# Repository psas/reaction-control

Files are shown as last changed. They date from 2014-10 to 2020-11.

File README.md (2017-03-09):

reaction-control
================

## Overview
We want active stabilization for LV3, but wish to escape the vexxing dynamic pressure limitations of the present aerodyamic canard based [roll-control system](https://github.com/psas/roll-control) used on LV2.3.

The concept:
* Cold-gas rocket propulsion
* 8 N thrust (roll), 11 N (pitch x, y)
* Nitrogen tank at 4500 psi
* 8x 3D-printed bell nozzles
* PWM throttling
* "Robust control"

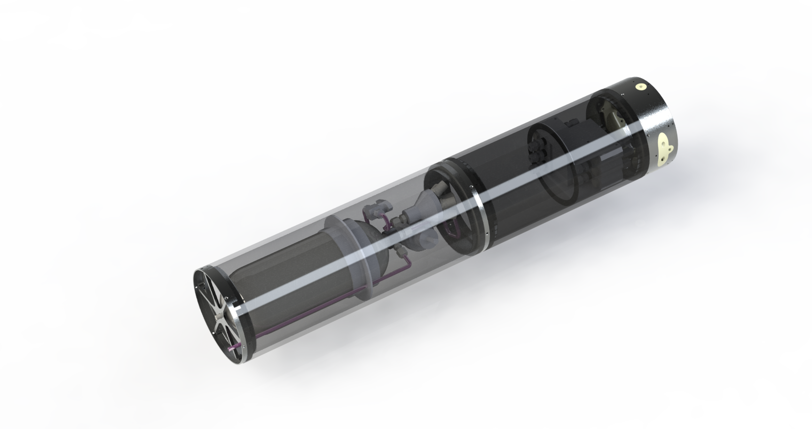
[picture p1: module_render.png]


Rao bells (e.g. nearly ideal nozzles) are hard to machine c.f. conical nozzles, but easy to 3D print. This also enables “plug & play” optimal expansion ratios for any trajectory. Here is the basic workflow:
* Determine flight envelope from simulation (for instance, using [OpenRocket](https://github.com/psas/lv3.0-airframe/tree/master/sim/ORK))
* Run `nozzle_sizing.m` script to determine nozzle design parameters
* Plug expansion ratio into parametric solid model and export `.stl`
* Print nozzles, install in carrier ring
* ???
* Fly!

This repo includes mathematical models, matlab and python controller scripts, eagle files for a custom MOSFET relay board, solenoid PWD test data for transfer functions, system test data and bode analysis, and the Solidworks CAD assembly for the LV3 Reaction Control System.

## Suplimentary Links
[Link to AIAA SPACE 2015 presentation slides](https://docs.google.com/presentation/d/1vfhgjRymidfKbpzjqC0tfAL57iSsNFOEQSFTw5_EEGs/edit?usp=sharing)

[Link to AIAA SPACE 2015 conference proceedings paper](https://github.com/psas/reaction-control/blob/master/pubs/AIAA%20RCS%20Manuscript_FINAL2.pdf)

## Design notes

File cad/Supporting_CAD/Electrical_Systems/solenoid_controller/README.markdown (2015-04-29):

# Solenoid Controller Board

A breakout board to drive the solenoids with GPIO from any microcrontroller.

## Schematic

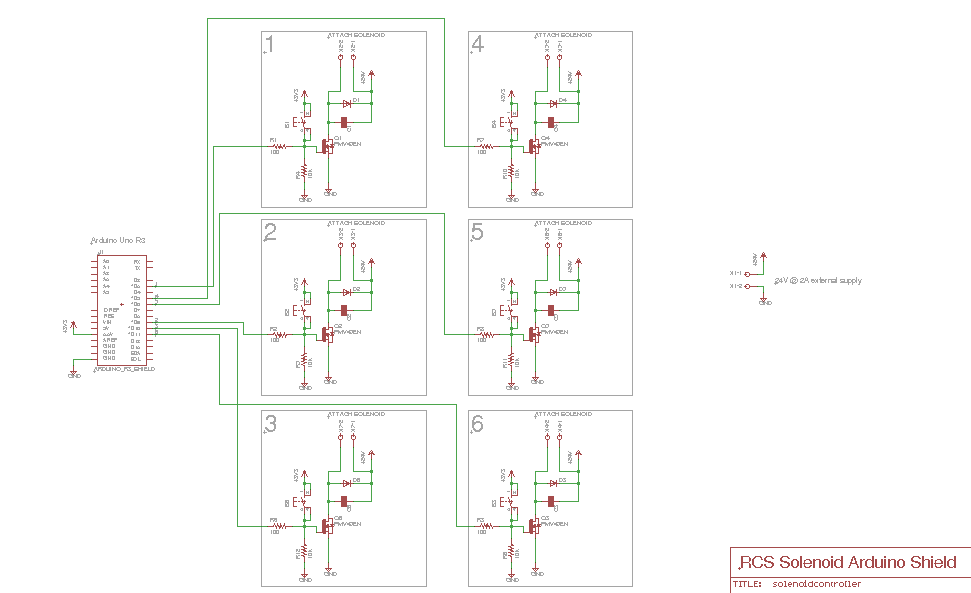
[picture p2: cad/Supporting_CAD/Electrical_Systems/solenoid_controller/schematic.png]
schematic


## Board

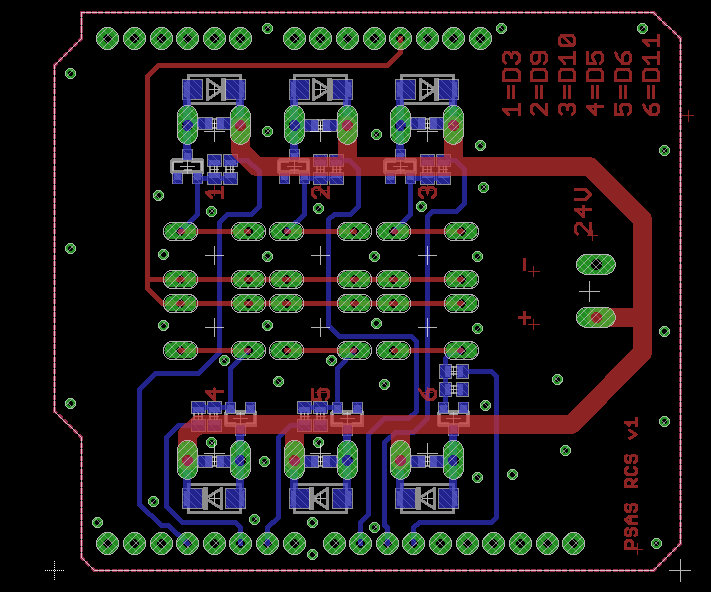
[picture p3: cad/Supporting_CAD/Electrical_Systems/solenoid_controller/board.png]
board


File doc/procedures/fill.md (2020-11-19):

# RCS Fill Procedure
## Notes
- The fill system definitely needs a choke to prevent over-filling the RCS and reduce the fill rate.
    - We may want to put a cold sink on that choke and monitor its temperature during testing.
- We probably want to define a standard way to clean fittings and dust covers,
  so we aren't repeating it in the procedure.
## Nomenclature
- "Caution" = potential damage to equipment
- "Danger" = potential damage to people (and potentially equipment).
- "FOD" = Foreign Object Debris (anything that shouldn't be there, e.g., dirt, metal shavings, grease, water, stray tools)
- "PPE" = Personal Protective Equipment
- "NOID" = NO IDentifier
    - Anything marked with NOID needs an identifier in the procedure and system-level illustration.

## Required Materials
| Quantity | Part Name | Identifier | Part Number
| --- | --- | --- | ---
| 1 | Compressed Gaseous Nitrogen Tank |  |  
| 1 | RCS Fill System |  |  
| 1 | impact-resistant safety goggles (TODO: ANSI standard) |  |  
| 1 | heavy hearing protection (TODO: ANSI standard) |  |  
| 1 | dry cloth |  |  
| 1 | fill tank transportation cart |  |  
| 1 |  |  |  
| 1 |  |  |  
| 1 |  |  |  
| 1 |  |  |  

## General Precautions
- The internal components of the RCS and its fill system are sensitive to FOD.
    - It's important to keep work areas clean to avoid contamination.
- The fill tank is nominally pressurized to (TODO) atmospheres and stores an equivalent energy of (TODO) kg TNT.
    - This is enough to (TODO: look up medical hazards) and eject FOD/shrapnel.
    - People must wear the above-listed PPE when within (TODO: safe radius) of the fill tank when it is pressurized.
- The RCS is nominally pressurized to 238 atmospheres and stores an equivalent energy of 27.1 g TNT.
    - This is enough to (TODO: look up medical hazards) and eject FOD/shrapnel.
    - People must wear the above-listed PPE when within (TODO: safe radius) of the RCS when it is pressurized.
- If you get unexpected results at any point during this procedure, stop and reevaluate what's happening.

## Operations
### Fetching the Supply Tank
1. TODO: instructions on how to remove the tank from its storage location.
1. TODO: instructions on how to transport the tank.

### Installing the Supply Tank
1. TODO: instructions on how to secure the tank to the fill system.
1. Remove the protective cap from the fill tank.
1. Ensure (NOID: tank connector) is free of FOD. (TODO: cleaning)
1. Remove the dust cover from (NOID: supply end of fill sys) on the fill system.
1. Ensure (NOID: supply end of fill sys) is free of FOD. (TODO: cleaning)
1. Connect (NOID: tank connector) to (NOID: supply end of fill sys). (TODO: specific instructions)

### Connecting to the RCS
1. Remove the dust cover from (NOID: RCS side of fill sys).
1. Ensure (NOID: RCS side of fill sys) is free of FOD.
1. Remove the dust cover on (NOID: RCS fill port).
1. Ensure (NOID: RCS fill port).
1. Connect (NOID: RCS side of fill sys) to (NOID: RCS fill port) such that there is an audible click.

### Filling Proper
1. Ensure `Reg-02` is fully closed. (TODO: direction/instructions)
- Danger: 
    - The next step will pressurize part of the fill system to the same pressure as the fill tank.
    - If `Reg-02` is not closed, it may over-pressure the RCS tank, damaging or exploding it.
    - If the couplings of the fill system aren't secure, they may turn into thrusters.
2. Open `HV`. (TODO: expected feedback?)
    - You should not see any pressure rise in (NOID: RCS-side gauge).
    1. If you see a pressure rise in (NOID: RCS-side gauge), close `HV` immediately and reassess.
- Danger: 
    - If you open `Reg-02` by too much in the next step, it could over-pressure the RCS tank, damaging or exploding it.
3. Open `Reg-02` by 0.25 turn. (TODO: good increment?)
    - You should hear a hissing sound from the regulator.
4. Wait for the reading of (NOID: RCS-side gauge) to stabilize.
    - The hissing sound should stop as the pressure stabilizes.
    1. If you hear `PRV-02` start hissing or you see (NOID: RCS-side gauge) exceed 3500 psi:
        1. Close `Reg-02` immediately.
        1. Close `HV` immediately.
        1. Reassess.
        1. Return to step 1 of "Filling Proper"
5. If the reading of `Reg-02` is below 3400 psi, repeat steps 3 through 5 of "Filling Proper".
    - (NOID: RCS-side gauge) should now read between 3400 and 3500 psi.
1. Close `Reg-02` completely. (TODO: direction?)
1. Close `HV` completely. (TODO: direction?)

### Disconnecting
1. Ensure the dust covers for (NOID: RCS-side of fill sys) and (NOID: RCS fill port) are free of FOD.
- Danger: If `HV` is not closed, the next step may turn (NOID: RCS-side of fill sys) into a thruster.
1. Loosen (NOID: RCS-side of fill sys) from (NOID: RCS fill port), but do not disconnect them.
    - You should hear a hissing sound.
1. Wait for the pressure in (NOID: RCS-side gauge) to drop to 0 psi.
    - The hissing sound should stop.
1. Open `Reg-02` slowly until you hear a hissing sound.
1. Wait for the pressure in (NOID: fill-side gauge) to drop to 0 psi. (TODO: is there some residual pressure left by Reg-02?)
    - The hissing sound should stop.
1. Disconnect (NOID: RCS-side of fill sys) from (NOID: RCS fill port).
1. Replace the dust covers of (NOID: RCS-side of fill sys) and (NOID: RCS fill port).

### Returning the Supply Tank
1. Ensure the dust cover of (NOID: supply-side of fill sys) is free of FOD.
1. Disconnect (NOID: supply-side of fill sys).
1. Replace the dust cover on (NOID: supply-side of fill sys).
1. Replace the protective cap on the supply tank.
1. TODO: instructions for moving the supply tank to the cart

### Fetching the Supply Tank
1. TODO: instructions on how to transport the tank.
1. TODO: instructions on how to secure the tank in its storage location.

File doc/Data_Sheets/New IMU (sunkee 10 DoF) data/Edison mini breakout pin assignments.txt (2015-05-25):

I2C-1:
SCL = j18-pin6 (gp19)(I2C-1-SCL)
SDA = J17-pin8 (gp20)(I2C-1-SDA)

Power and Ground:
GND = j19-pin3
Vin(7-15V) = j17-pin4
sys input power(3.15-4.5V) = J20-pin1
3.3V = j20-pin2
1.8V = j19-pin2

I/O:
     solenoids 1-6:
	j20-pins 10,9,6(GP 41,42,49)(MRAA 51,50,47)(arduino 10,12,8)
	j19-pins 10,11,6(GP 40,43,48)(MRAA 37,38,33)(arduino 13,11,7)
     Leds:
	Armed: j18-pin7 (GP 12)(MRAA 20)(arduino 3)
	Running: j18-pin1 (GP 13)(MRAA 14)(arduino 5)
     E-stop:
	j17-1 (GP 182) (MRAA 0) (arduino 6)

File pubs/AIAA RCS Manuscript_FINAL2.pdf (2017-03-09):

1 Student, Maseeh College of Engineering, Student Member 2 Student, Maseeh College of Engineering, Student Member 3 Student, Maseeh College of Engineering
4 Student, Maseeh College of Engineering, Student Member 5 Student, Maseeh College of Engineering, Student Member

American Institute of Aeronautics and Astronautics

# Development of a Low-Cost, Open-Hardware Attitude Control System for High-Powered Rockets

Erin Schmidt¹

, Jeremy Louke²

, Kenneth Arnell³

, Jeffrey Hickman⁴

, and Brentley Wiles⁵
Portland State University, Portland, OR 97201

Attitude control systems are an important enabling technology for amatuer and university class high-powered rockets to be more useful as platforms for high-altitude science, but are presently too costly and technically complex to implement for many groups. With the intention of making this technology more accessible to the high-powered rocketry field a mechanical engineering senior capstone team at Portland State University developed an open-source, scalable attitude control system leveraging COTS components, robust controls, and additive manufacturing. A qualitative narrative describing the system design process is presented here.

Nomenclature
COTS = Commercial Off The Shelf
DoF = Degree of Freedom
IMU = Inertial Measurement Unit
LQR = Linear Quadratic Regulator LTI = Linear Time Invariant
PSAS = Portland State Aerospace Society PWM = Pulse Width Modulation
RCS = Reaction Control System
I. Introduction
The Portland State Aerospace Society (PSAS) is an engineering student group and citizen science project at Portland State University dedicated to building low-cost, open-source, and open-hardware high-powered rockets and avionics systems. The group’s stated long term goal is to place a 1 kg cubesat into low Earth orbit with their own launch vehicle. This goal is set amidst the incredibly rapid expansion of the small satellite industry in this decade. Between 2013 and 2014 launches of nanosatellites, defined as satellites in the 1-10 kg mass range, increased by 270% according to SpaceWorks Small Satellite 2014 annual market analysis. Presently the small satellite market is handicapped by the limited selection of dedicated launch services options; satellite operators must choose between launch rideshares as a secondary payload (either on commercial launches or through NASAs Cubesat Launch Initiative) or deployment from the ISS Nanoracks system. In either case the satellite operator must cede ultimate control over the satellite orbital parameters to the launch services provider’s primary customer. Because this place a substantial limitation on the utility of small satellites a number of efforts are currently underway to develop dedicated launch vehicles to service the small satellites market, including a NASA request for proposals for “Venture Class Launch Services” capable of inserting up to 60 kg of U-class satellites (e.g. cubesats) into Low Earth Orbit. One fundamental technical requirement for these orbital rockets is a system for guiding the rocket along an orbital insertion trajectory; such systems are known as attitude control systems.

Dedicated small satellite launch vehicles share cladistic similarities, at the extrema of their range, with both large orbital launch vehicles and the comparatively small high-powered rockets that have been operated by hundreds of amateur and university groups such as PSAS, for decades. Typically high-powered rockets fly ballistic trajectories with apogees nearly always less than 30 km and more commonly less than 10 km altitude. However, several of these amateur and university groups harbor aspirations of sub-orbital flight above the von Karman line. In the context of amateur and university high-powered rocketry groups, attitude control systems have many near-term potential applications and usage cases:
1. active stabilization,
2. trajectory control, dispersion envelope control and range safety,
3. science, payload, and instrumentation requirements,
4. atmospheric reentry energy management,

One direct application of an attitude control system in high powered rocketry is counteracting the deleterious effects of weather cocking (that is, the tendency of rockets to steer into the wind). Aerodynamic fins are often used in conjunction with nose cone weights to ensure the rocket’s center of pressure is well behind the center of mass such that corrective moments are produced for non-zero angles of attack. Weather cocking is a side effect of this need to use large fins for passive stabilization. Local wind speeds change the fluid velocity vector so that it is no longer strictly vertical for a rocket in flight. Ultimately this causes rockets to squander impulse in accelerating laterally. By using an attitude control system for active stabilization fin sizes can be reduced and the high-powered rockets maximum altitude at apogee can be improved.
Relatedly, very high altitude launches are constrained by range safety issues. Generally obtaining a FAA waiver for a Class 3 ‘Advanced High-Powered Rocket’ launch is contingent on being able to rigorously justify that the rocket will return to the Earth within some radius of the launch site that is safely distant from populated areas. This area within which the rocket must land is called the dispersion envelope. Unfortunately, ensuring an acceptably small dispersion radius becomes more and more difficult with increasing altitude at apogee, both due to weather cocking and the tendency of high altitude winds to translate the launch vehicle downrange. This introduces a novel usage case for an attitude control system. Using a combination of publically available NOAA data on high altitude winds and Monte Carlo simulation an initial heading and launch angle can be determined that will cause the rocket to land very near the launch site with a known level of statistical confidence. Using this information the boost guidance on the launch vehicle would, upon clearing the tower, immediately roll to align one of the pitch axes with the desired heading and then pitch over to the initial launch angle. This is known colloquially as “calling the shot”, and would be unprecedented as an in-situ capability for a launch vehicle in the high powered rocketry class. Presently such capability is attained by gimballing the entire launch tower rail.¹
In addition to boost guidance, rocket
attitude control enables support for
sensors or instrumentation with specific
angle or rate pointing requirements. For large suborbital sounding rockets a significant portion of the flight time is spent above the atmosphere (often as long as five minutes). At this altitude, free-fall
conditions | prevail | and | perturbing
aerodynamic torques are small such that an attitude control system can provide a stable actively pointed platform for experimentation with minimal disruption from controller vibrations. Research areas that benefit from such technology
include | microgravity | fluid | physics,
meteorology and atmospheric science, infrared and x-ray astronomy. Should an
inexpensive, | open-hardware | attitude
control system be developed that is scaled for university class sounding rockets, then some of these rockets may
eventually | be | evolved | into | more

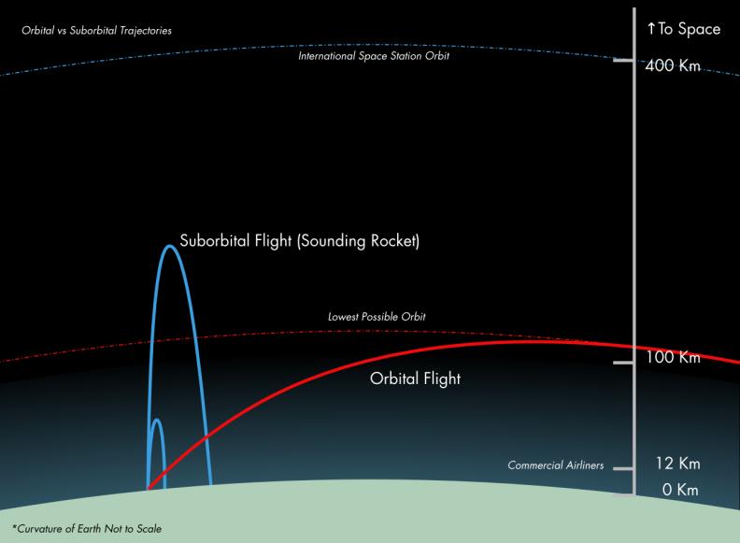
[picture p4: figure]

Figure 1. Comparative schematic of orbital and suborbital trajectories (image courtesy of PSAS).

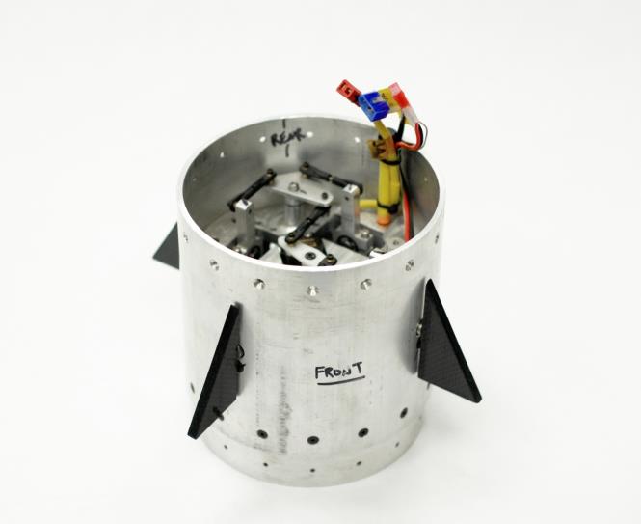
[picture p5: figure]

generally capable platforms for research in these fields. Other payloads and subsystems can benefit from directional pointing as well, such as cameras and telemetry downlink antennas.
Another application is energy management during payload reentry. During the atmospheric reentry phase of a suborbital trajectory enormous heat and dynamic pressure loadings develop as the launch vehicle decelerates from several kilometers per second ground relative velocity. Mitigating the
effect | of | these | loadings | is | critical | for
comparatively small scale single-stage launch vehicles that are intended to be recovered and reused, such as many university group operated high powered rockets. An attitude control system can be used to place an initial spin on the launch vehicle; as it reenters the atmosphere aerodynamic drag induces small torques on the spinning vehicle. Because of rotational energy dissipation, these small torques cause the spin to precess or nutate to the axis with the highest moment of inertia, in this
case | the | pitch/yaw | axes. | This | flat-spin
aerodynamic mode has the effect of increasing drag coefficients for the launch vehicle. The resulting increase in drag can be harnessed to bleed off excess velocity of the vehicle during reentry at an acceptably low dynamic pressure.
A yet more ambitious application of boost guidance and attitude control is trajectory optimization for orbital launches. Ascent trajectories for orbital launch vehicles differ in several key respects from sounding trajectories which otherwise do not require inertial guidance; these are schematically illustrated in Figure 1. Optimal ascent trajectories are designed to minimize overall launch delta-v requirements, however this is difficult because the relative magnitude of various losses, such as drag, gravity and steering losses are path dependent. Active control thus becomes a powerful tool for optimizing orbital launch trajectories.
Inside Earth’s atmosphere the most often used attitude control strategy is to actuate steerable aerodynamic control surfaces, such as fins or canards. Unfortunately, such systems are constrained by the dynamic pressure at which they can produce useful amounts of lift. Generally, this corresponds to a limiting flight envelope of about 30 km altitude.

Figure 2. LV2.3 Roll Control System (image courtesy of PSAS).

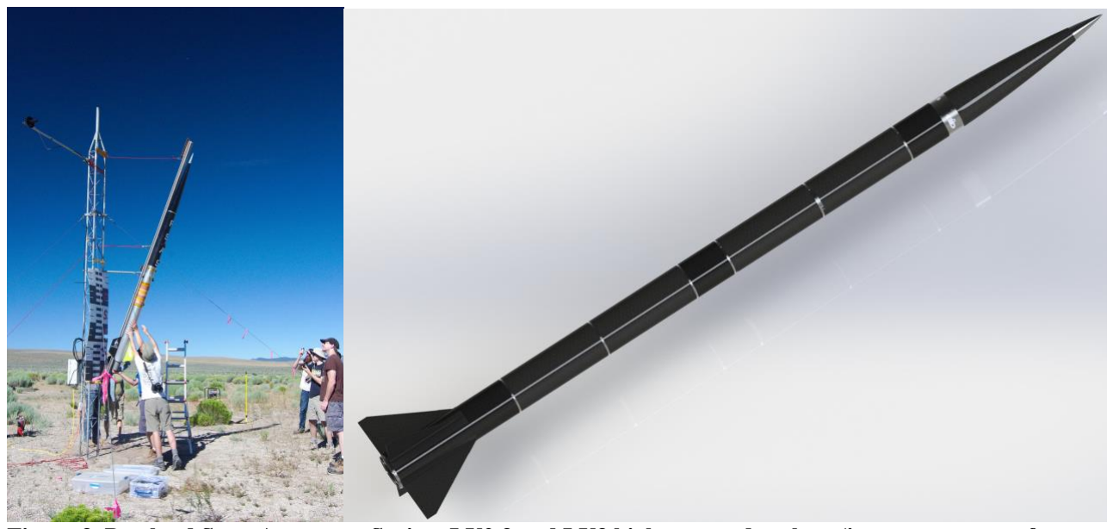
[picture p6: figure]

Figure 3. Portland State Aerospace Society LV2.3 and LV3 high powered rockets (images courtesy of PSAS).

PSASs current generation sounding rocket, LV2.3, is capable of a 5 km apogee and low supersonic velocities. It uses a module with servo-actuated steerable canards for roll axis attitude control, shown in Figure 2. In 2014 PSAS began work on a new very high-altitude high powered rocket, the LV3, with a design apogee of over 40 km. These vehicles are pictured in Figure 3. Pursuant to their mission of developing inexpensive, open-source technologies for small-scale orbital launch vehicles PSAS issued a call for a 6 degree of freedom attitude control system which could operate at these very high altitudes. This became the basis of a mechanical engineering senior capstone project at Portland State University.

II. Top-Level Design
A. Requirements
The essential design requirement for the attitude control system is that it must control the launch vehicle pitch, yaw and roll angles and velocities at all conceivable altitudes and in vacuum conditions, with particular emphasis placed on the roll axis. The system should have at least 150 N•s of stored impulse. The system should use inexpensive COTS components. The system should also be expressly designed with extensibility and scalability in mind. This requirement follows from PSASs general
interest in open-source development of
technologies for high powered rocketry, and the
fact that LV3 is presently in the preliminary design phase and its mass characteristics and trajectory design are still subject to change.
B. Baseline Design
The baseline attitude control system design is a cold-gas vernier jet type Reaction Control System (RCS) as seen in Figure 4. The RCS module is designed to fit ⌀6.o” payloads. The RCS module itself is physically composed of a high-pressure nitrogen propellant tank, a regulator, a series of 6 solenoid valves (two for roll, and four for pitch/yaw) plumbed to 8 3D printed rocket nozzles, a power supply and MOSFET relay board, an Intel Edison microcontroller with an Arduino breakout board, an inertial measurement unit, a set of pressure transducers, miscellaneous plumbing (gas lines, push to connect fittings, compression fittings, a fill valve, a latch valve, a high pressure tank adaptor, a gas distributor manifold, burst disks, etc.) a structural frame, and a carbon-composite aeroshell. The set of 8 vernier jet rocket nozzles are arranged such that they are perpendicular to the 3 principle axes of rotation of the rocket. When the solenoids are energized nitrogen gas exhausts supersonically through the rocket nozzles producing thrust. These thrust forces act across a lever arm to the vehicle center of mass to produce moments of force which then steer or orient the vehicle in whatever direction is desired. Cold-gas propulsion systems, while of generally low performance, are inexpensive, mechanically simple, and safe to operate such that they can be used by high turnover university student groups. The open-source/open-hardware and scalability requirements for different missions led to the selection of a modular system layout

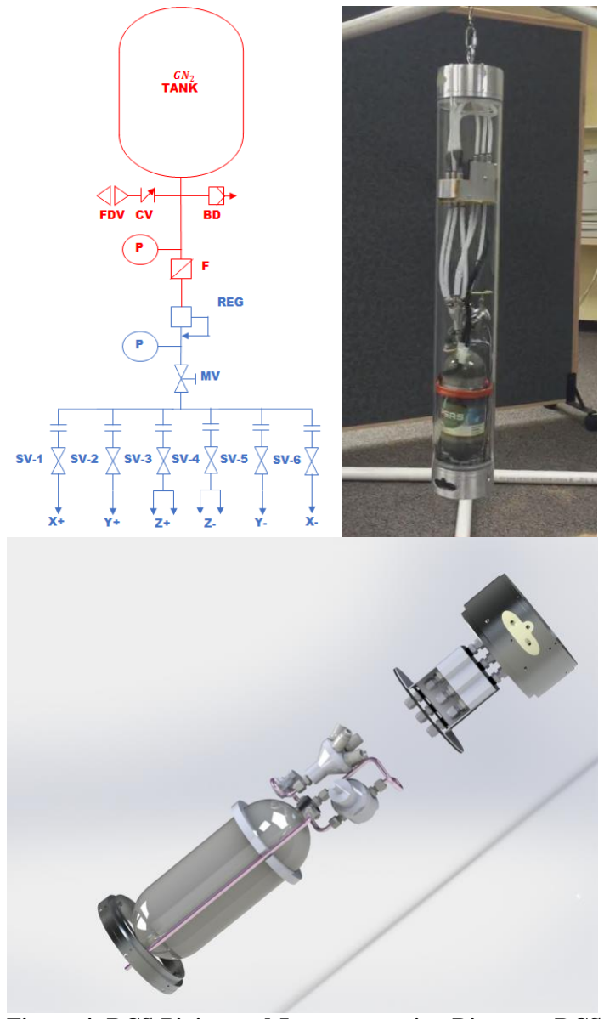
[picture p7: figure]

Figure 4. RCS Piping and Instrumentation Diagram, RCS roll test module in acrylic display case, and Solidworks® render of RCS assembly.

with 3D printed nozzles, and a controller robust enough to tolerate large variances in system dynamics and model uncertainty, and that is relatively straightforward to determine gains via simulation.

III. Propulsion
Nitrogen cold-gas has comparatively low theoretical specific impulse of about 70 s at 100 psi chamber pressure and standard temperature. This means that the ratio of mass flow rate to developed thrust is high and thus is inefficient. Since there are both volume and mass constraints on the total amount of propellant that can be carried on the rocket some analysis was required to optimize nozzle performance where possible. Additionally for a scalable, open-source system a way is required to ensure that the numbers that are put into the plant model in the controller are accurate. An essential property of rocket nozzles is that their design expansion ratio is optimum for only a single ratio of back pressure to chamber pressure. This optimal performance therefore corresponds to a single specific altitude of operation. Problematically, for any sub-orbital sounding trajectory the altitude, and thus the back pressure, changes rapidly with time. One primitive, but analytically straightforward approach to determining the back pressure is simply to use an averaged ‘characteristic altitude’ value associated with a mission design flight envelope in combination with the US 1976 standard atmosphere model. Using additive manufacturing techniques we gain the flexibility to rapidly manufacture optimal nozzles on the fly to fit any specified mission trajectory, or launch vehicle mass characteristics by varying nozzle throat area, and
expansion ratio parameters.
An ideal nozzle is shaped such
that all flow is axial at the exit plane, eliminating divergence
losses, | however | such | ideal
nozzles are infinitely long and so cannot be used for practical propulsion. Since 1960 Rao’s
method | of | characteristics
approach has been used to
analytically | determine | the
contour | needed | to | achieve
optimal (i.e. uniform parallel) flow conditions at the exit plane.² This requires that flow be inviscid and 2-D, however since real flow is viscous a boundary layer correction must be applied ex post facto. For large rocket nozzles these losses are comparatively small (generally less than 1.0 %).

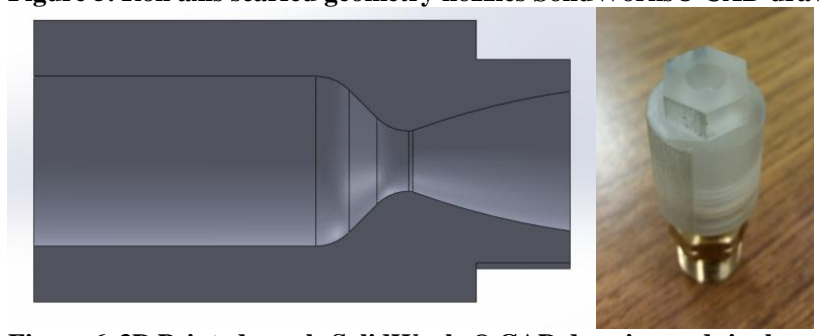
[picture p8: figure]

3
Nozzles with throat Reynolds numbers greater than 10⁶
are not
believed to have significant boundary layer losses.⁴,5 For small nozzles there is potentially a much larger effect.
The Rao perfect nozzle is not a parabola, however it resembles
one and can be reasonably be
approximated | as | one. | Such

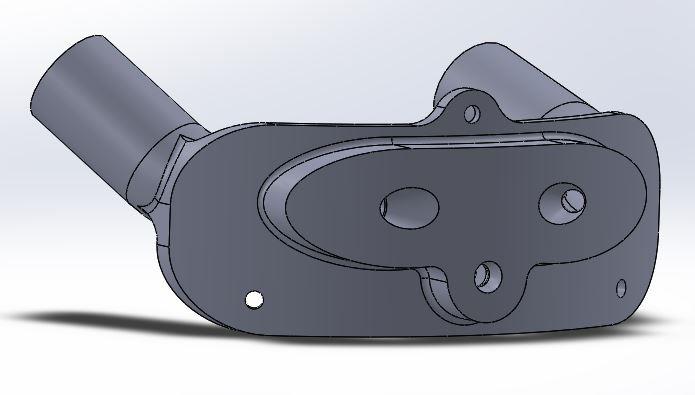
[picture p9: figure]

nozzles are commonly termed ‘Bell nozzles’. These nozzles can be shorter than conical nozzles of equivalent expansion ratio. The significant divergence losses in conical nozzles can only be reduced by reducing the divergence angle. For the same expansion ratio this means that the nozzle will have to be longer. As the 3D printed nozzles are real rather than ideal nozzles, added length has the effect of increasing boundary layer and frictional losses, which are compounded by the combination of small throat area, rough interior surface finish and low chamber pressure. A further advantage of additive manufacturing in that it enables use of the Rao bell paraboloid nozzle which are normally difficult to manufacture at very small scales using conventional machining techniques.

Figure 5. Roll axis scarfed geometry nozzles SolidWorks® CAD drawing.

Figure 6. 3D Printed nozzle SolidWorks® CAD drawing and single-stream test nozzle.

A simple procedure was developed which makes this approach very easy to scale. First, the known back pressure and desired thrust are used as arguments in a simple MATLAB® script to determine throat area and optimal expansion ratios for the RCS nozzles. Initial and final angles, and convergence radii of the ideal Rao paraboloid approximation are determined from a lookup table using the expansion ratio and percent bell.³ These values are input into a SolidWorks® parametric model of the rocket nozzles. As the RCS module is inline, nozzles were scarfed, as seen in Figure 5, to conform to the airframe outer diameter. This unfortunately incurs a small cosine loss as the thrust vector is no longer coplanar with the nozzle axis of radial symmetry. Effective expansion ratios for the scarfing were determined using a straightforward root mean square approach.⁶ Lastly SolidWorks® is used to export “.stl” files that can be sent to any commercial 3D fabricator for printing. The RCS nozzles were printed on a 3D Systems ProJet® 3500 HD Max printer. The production media, VisiJet Crystal, is relatively durable, and can be tapped for threaded inserts or fittings. An example of a 3D printed test nozzle can be seen in Figure 6.
The first major step in the nozzle design process was determining the thrust level required of the system. Starting with the equation of motion

Iθ̈= T
(1)

where I is the mass moment of inertia, θ̈is the angular acceleration, and T is the torque. Furthermore, torque is defined by the equation,

Fr = T
(2)

where F is thrust force and r is lever arm (i.e. launch vehicle outer radius). Substituting (2) into (1) leads to the equation for the required thrust force (uncoupled)

F =

Iθ̈
r

It was desired for LV3 to be able to conduct snap rolls off of the tower to support the “call the shot” usage case. This called for a maximum case 45˚ roll program to be completed in 1 s, requiring 0.80 rad/s² of angular acceleration. Given this value, and the worst case expected values of mass moment of inertia and lever arm of LV3 in roll, the thrust required from the roll nozzles is only 6.0 N.

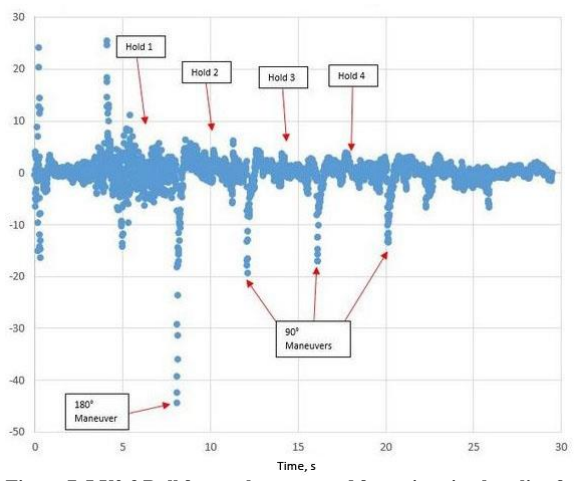
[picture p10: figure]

Figure 7. LV2.3 Roll force telemetry used for estimating baseline for RCS performance.

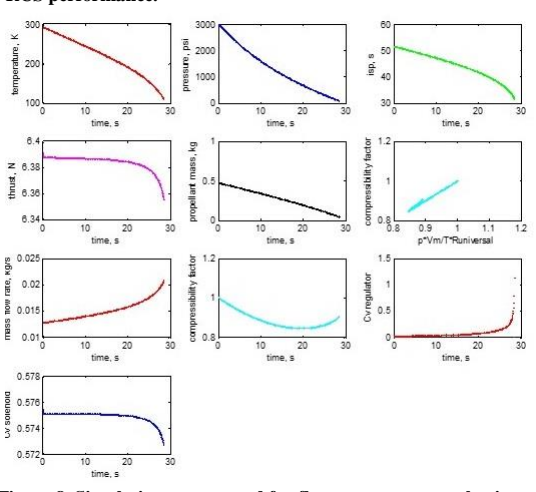
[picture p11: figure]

Figure 8. Simulation output used for flow componentry selection.

Another design consideration is an estimate the required delta-v for maneuvering and active attitude stabilization, which is important for trade off analysis of rocket fin size as well as propellant tank size. Unfortunately there does not seem to be a straightforward analytical approach to determining impulse budgets for launch vehicle attitude control. Therefore the impulse budget, along with the magnitude of dynamical perturbations affecting the airframe generally, was estimated using launch telemetry from PSASs LV2.3. It was determined that the average perturbing force acting on LV2.3 was 1.49 N. Integrated over a 30 second period of active control this translates to required impulse budget of 45 N•s to maintain roll rates at 0 rad/s²
, neglecting any additional planned maneuvers. Given an initial tank pressure of 3500 psi and isothermal emptying conditions this translates to a required tank volume of 0.885 L. A roll force plot constructed from LV2.3 telemetry is presented in Figure 7. It is desirable that the ratio T/I be large enough to zero out initial rates to the satisfaction of any response time requirements, and to exceed the magnitude of any expected disturbing torques by a large margin, but yet no so large that attitude hold fuel-efficiency is negatively affected with a sub-nominally damped control response. Based on the assumption that the disturbing torques are similar between LV2.3 and LV3 a design thrust of 8.0 N was chosen for the RCS roll nozzles. The propellant tank is a Luxfer composite 2 L cylinder with a specified service pressure of 4500 psi. Given a design pressure of 3500 psi the tank should have a mission impulse budget factor of safety of close to 2.
Additional simulations of tank and nozzle thermodynamics were used to determine required flow coefficients for the various flow components in the system, particularly of the solenoid valves and the pressure regulator. The model used discrete time iteration to model the changing tank conditions using the Van der Wall equations of state and the isentropic relations, in addition to the non-choked flow coefficient equations. This was done to ensure that choked flow conditions would hold only at the nozzle throat and thus that the nozzle would operate supersonically. This helped inform the COTS component selection of the detailed design phase of the engineering process. An example model output plot for the case of a flight-like nozzle with a 100 psi chamber pressure nozzle operated at sea level with an expansion ratio of 2, inlet temperature of 290 K, initial tank pressure of 3500 psi, and a throat area of 1.26x10⁻⁵ m² is
shown in Figure 8. These simulations indicated that for the isentropic tank emptying condition at the expected duty cycles, and initial conditions propellant temperatures would rapidly drop to the region 70-90 K. This is close to the saturation temperature of nitrogen at 1 atmosphere. Though it was understood that the tank would not empty in a purely isentropic mode, a naively applied lumped capacitance analysis of the thermal response of the solenoid valves was conducted. This analysis conservatively assumed that only the solenoid armature absorbs heat, and made use of the Dittus-Boelter Nusselt number correlation (i.e. assuming that the flow is turbulent and fully developed though the solenoid). It was determined from this analysis that Biot numbers were large and that the characteristic time was of the same order of magnitude as the solenoid open time. This led to the selection of solenoid valves with Buna-N seals, which are expected to maintain integrity against leaks at temperatures as low as -40 C.

IV. Controller
A. Modeling
For the rotational tests, a simple proportional controller was used. This controller satisfied the key requirements without adding unnecessary complexity to the overall system. The creation of the RCS roll controller is broken into two methods: the theoretical modeling of individual blocks formed into a working system, and the physical implementation of the model applied to the dynamic mechanical system. The model consists of 5 major blocks, the DC limiter, controller, PWM generator, solenoid model, and the rotational system transfer function (e.g. the rigid-body dynamics of the airframe). The system model is shown in Figure 9.

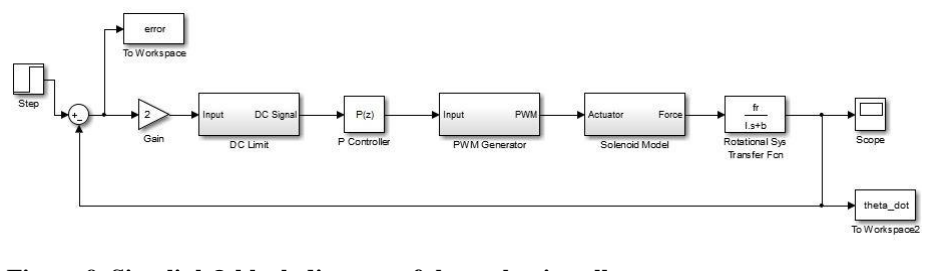
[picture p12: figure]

Figure 9. Simulink® block diagram of the rocket in roll.

A simplified transfer function, dubbed the flying cylinder, was created using system dynamics equations with respect to roll rate and disturbance force. Starting with the equation of motion and solving for the transfer function with the input as angular velocity and the output as force we obtain

θ̇
F

=

r
Is + b

where θ̇ is the rotational velocity, F is the force, r is the radial position of the nozzles, I is the mass moment of inertia about the rotational axis, b is the damping ratio of air, and s is the Laplace frequency domain variable.
The On/Off solenoid valve block, used as the actuator, is modeled with the equation

1
τs + 1

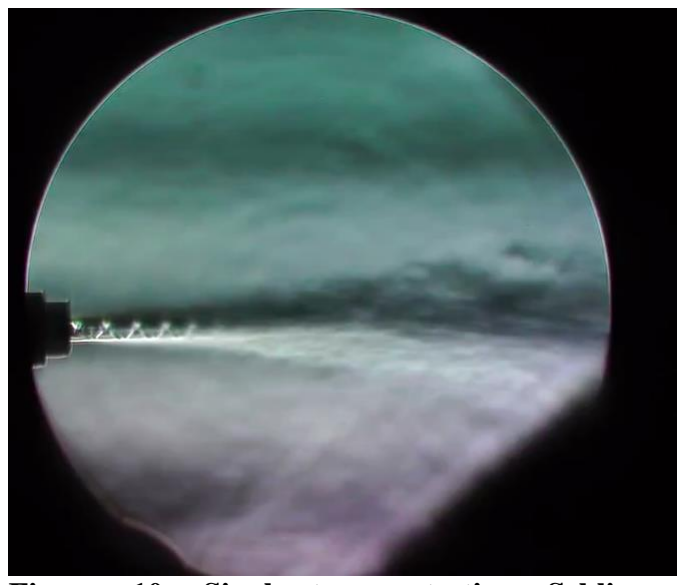
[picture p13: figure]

where τ is the solenoid time constant; this model was used to simulate the discrete time lag of the solenoid. The time constant was determined through the manufacturer’s lag time claims and verified by single-stream testing the system. A PWM block was also included to simulate the force out of the solenoid as it is cycled. This then had to be normalized from a 0 to 1 range (PWM duty-cycle). A PWM frequency of 5 Hz was selected by optimization between the fastest response time and widest duty-cycle range. A duty-cycle of 10% was determined to be the fastest rate at which the solenoid could be reasonably pulsed at 5 Hz, to achieve low-end force control (i.e. to minimize the size of the smallest impulse bit).
The DC limiter constrained the
control duty-cycle to a workable range,
from 10% to 80% pulse width. This block transforms the required thrust force into solenoid duty cycle by use of a linear regression determined through PWM single-stream testing of the propulsion system. The range of the workable low-end duty-cycle was determined through thrust force data
collected | during | single-steam
propulsion testing using a load cell, and through qualitative analysis of the transient developing flow during PWM solenoid operation using Schlieren interferometry, as seen in Figure 10.
This | single-stream | analysis | also
included characterization of the open and close lags, time constant, and controllability of the duty-cycles for the
solenoid. | The | maximum | thrust
developed by the nozzles was also
determined | through | single-stream
testing and compared to predictions from isentropic theory. The single-stream test apparatus is shown in Figure 11.

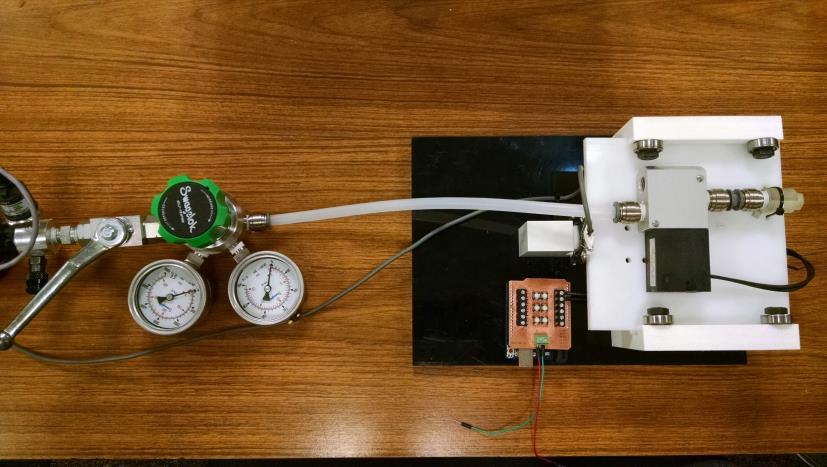
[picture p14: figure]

Figure 11. Single-stream test apparatus.

Figure 10. Single-stream testing Schlieren interferometry.

B. Implementation and Results
To help parallelize development, an open loop controller was initially used to qualitatively test the assembled system for operational performance, specifically scalable control forces, and equal forces from opposing nozzles. Additionally an LED simulator with full feedback control was rapily prototyped to qualitatively analyze the control law, sensor characteristics, and electronic system response. This proved useful quickly buying down development risk, identifying bugs, and avoiding unnecessary pressurization of the full roll-control RCS in advance of a test, which could be a time-consuming exercise. The feedback controlled simulator used an Arduino Uno microcontroller and a 6-DoF IMU (MPU-6050) for the on-board sensor. The 6-DoF LED simulator is shown in Figure 12. For the full roll-control RCS system an Intel Edison microcontroller was used in lieu of the Arduino Uno. Running the Ubilinux operating system, a Debian distribution targeted for use in embedded device applications, the RCS controller leveraged the Edison’s substantially improved performance and its wireless functionality. During captive wire-suspended tests a moment was applied to the rocket body, and the controller would then decrease the roll rate to zero. The data collected from the roll tests was then compared against simulation outputs. The roll rate accuracy was determined to be ±2 deg/s. The expected critical damping and settling time of under 80 ms from the model aligned well with the experimental test results as seen in Figure 13. The model is validated further by comparing model and experimental disturbance rejection as seen in Figure 14, simulating real world forces that are counteracted by the RCS. Using Bode analysis in MATLAB® we estimate that the controller has over -6 dB of gain and 60° of phase margin. This satisfies the robust control requirement, as the controller will tolerate dynamical changes in the plant and/or model uncertainty of over %50.

7

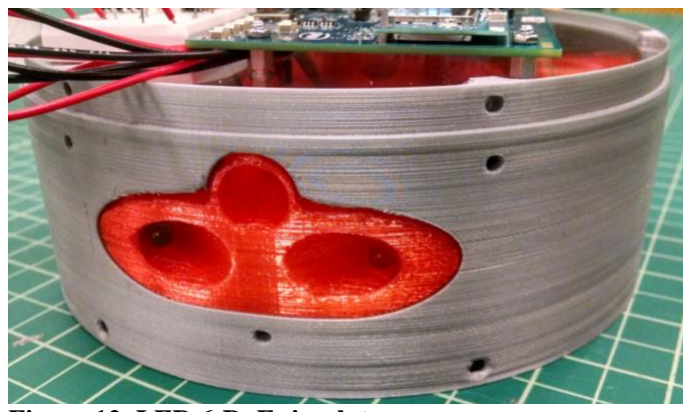
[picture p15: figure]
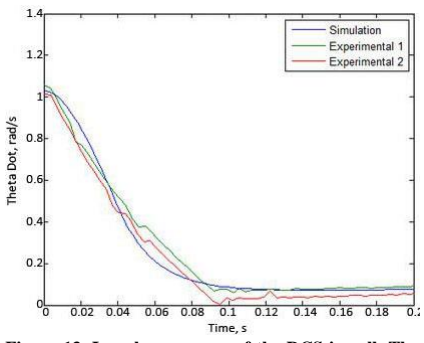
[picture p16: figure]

V. Ongoing and Future Work The RCS controller satisfies the baseline requirements outlined in the original project scope, however further development is necessary to enable robust 6-DoF control. Validating the roll model allows us to project the control logic to the pitch and yaw angles. A rigid-body 6-DoF dynamical model of the entire launch vehicle, shown in Figure 15, was developed in Simulink to provide a medium to simulate the rocket’s flight path and controller dynamics. This model contains multiple models that function as independent systems of the rocket throughout varying flight regimes; it serves as a stepping stone moving forward with the development of a fully controlled six degree of freedom RCS.

Figure 12. LED 6-DoF simulator.

Figure 13. Impulse response of the RCS in roll. The simulation data is plotted against the collected experimental data.

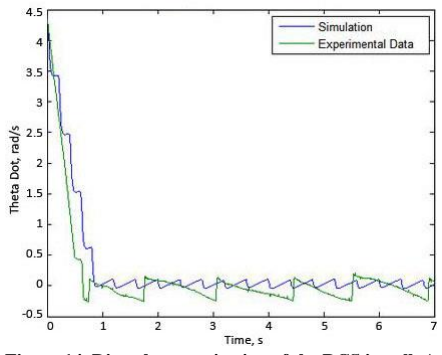
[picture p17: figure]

Following from the extensibility and scalability requirement is the planned implimentation of a Linear Quadratic Regulator (LQR) controller. This controller implementation is attractive due to their intrinsic robustness and ease of determining gains which are important advantages for a system that cannot be feasibly tested in physically realistic conditions prior to first flight. The ease of determining gains should also smooth the process of adapting the controller for use on other sounding rockets. Further capabilities enabled by LQR include gain scheduling via Linear Time Invariant (LTI) techniques, which has the potential to further improve the controller robustness as the fundamental dynamics of rocket flight change in different aerodynamic (subsonic, transonic transition, supersonic) regimes. While the rocket is not a Linear Time Invariant system, it can be modeled as one by scheduling optimized gains at different altitude ranges offering the more control authority over continuously changing flight conditions. Gain scheduling helps make the control logic tolerant of the time varying dynamics of the system plant. LQR also allows the use of cost minimization functions which provides an
elegant approach to preventing waste of the finite
supply of consumable propellant.⁸
To increase controllability of the system, state-space equations for rigid body attitude dynamics will be implemented; these can be found in some advanced aerospace controls texts.

9 They account for the damping on the rocket in different aerodynamic regimes. These can still be used effectively with the LQR controller. The controller can also be assigned a hierarchy of desired control states with varying weight. The controlled states consist of rotational position and velocity, translational position, and quaternions. Quaternion representations are useful in that they help avoid gimbal locking and account for dynamic cross coupling between different control axes. Further research is planned to model this behavior and implement it in the 6-DoF flight controller.

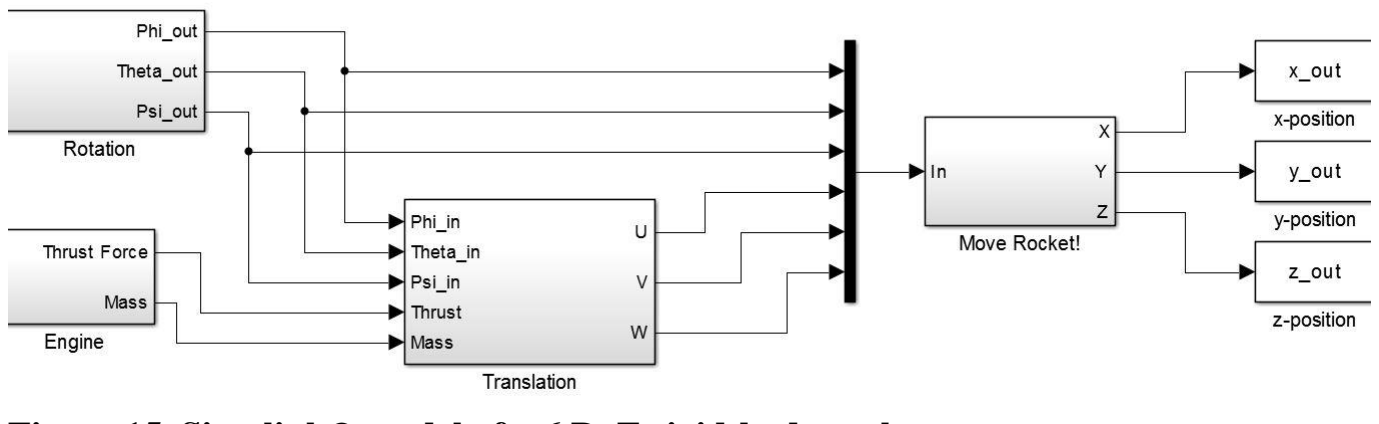
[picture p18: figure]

VI. Conclusion
As it stands the LV3 RCS is one of the only operational high powered rocketry class cold-gas attitude control systems in the world, and is also to the best knowledge of authors, the first such system designed entirely by a team of undergraduate students. The RCS module will be integrated on the PSAS LV3 stack for a demonstration flight in spring of 2016. Test risks associated with active control in the pitch/yaw axes will be mitigated by using the RCS in a roll control capacity only for its inaugural flight, however the system will be capable of full attitude control. Ultimately, there is very little inherently new in designing cold gas attitude control systems; such systems already have a very high technology readiness level. Currently attitude control systems are not widely used by university rocketry groups largely for cost and technical complexity reasons. However, in view of its many applications, RCS remains a key enabling technology for the burgeoning field of high powered rocketry and ultimately, low cost space access as well.

Figure 14. Disturbance rejection of the RCS in roll. A constant torque was applied to the RCS, inducing a constant disturbance. The controller was set to keep the angular velocity at zero. As shown in the disturbance rejection of error graph, the simulation closely models what is happening in the real world.

Figure 15. Simulink® model of a 6 DoF rigid-body rocket.

Acknowledgements
The authors are indebted to Dr. Ross Gadient and to the PSAS Advisors Andrew Greenberg, and Nathan Bergey for their support and advice. They are further indebted to Faculty Advisor Dr. Mark Weislogel for his advice and financial support. To ECE post-baccalaureates Aaron Baker and Kyle Lu for electrical engineering support. To PSUs Dryden Drop Tower Lab, and the Lab for Interconnected Devices for logistical support. To the PSU Beta Project for financial support as well as to the 60 PSAS crowdfunding campaign backers who raised over $10,000 to help fund the RCS capstone as well as four other 2015 PSU MCECS capstones. To Corwin Whitefield and 3D Fixtures Inc. for extremely generous 3D printing in-kind donations. To Advanced Flight Systems Inc. and the PSU ME Machine Shop for donated machine time and tooling. To instructibles.com and Intel for the donation of an Intel Edison development board.

Reference

1
Jung, W., Gomes, R. M., Louis, J. E., Neto, O. S., “Aeolus- Wind Weighting Program and Concept for Unguided Suborbital Launch Vehicles,” 19th ESA Symposium on European Rocket and Baloon Programmes and Related Research, ESA SP-671, 2009.
2Allman, J. G., and Hoffman, J. D., “Design of Maximum Thrust Nozzle Contours by Direct Optimization Methods,” AIAA Journal, Vol. 19, Jun. 1981, pp. 750–751.
3Sutton, G. P., Biblarz, O., Rocket Propulsion Elements, 7th Edition, New York: Wiley-Interscience, 2000, pp. 80, 87.
4Massier, P. F., Back, L. H., Noel, M. B., and Saheli, F., “Viscous Effects on the Flow Coeffcient for
a Supersonic Nozzle," AIAA Journal, Vol. 8, No. 3, March 1970, pp. 605-607.
5Brinich, P. F., Jack, J. R., and Spisz, E. W., “Thrust coefficients of low-thrust nozzles”, NASA TND-3056, 1965. 6Obrien, C. J., “Unconventional nozzle tradeoff study”, NASA CR-159520, 1979.

7
Jeb Orr, and Tannen Van Zwieten, “Robust, Practical Adaptive Control for Launch Vehicles,” AIAA Guidance, Navigation, and Control Conference, American Institute of Aeronautics and Astronautics, 2012.
8Martinez, C., “Digital attitude control for NASA sounding rockets,” Proc. SPIE 3442, Missions to the Sun II, 1998, pp. 157–165.
9Wie, B., Space Vehicle Dynamics and Control, Reston, VA: AIAA, 2008.

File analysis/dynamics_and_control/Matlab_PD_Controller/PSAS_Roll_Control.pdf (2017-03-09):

clear;
close all;

%constants taken from http://psas.pdx.edu/rollcontrol/
Izz = 0.08594; | %m2*kg
kd = .002; | %damping coefficient
kt = .9141; | %Nm/rad torsion rod spring constant exper. determined
lf = .0762; | %m distance from fin to z axis

%State Space equation
%assuming partial-state feedback (angular vel.) %model equation from http://psas.pdx.edu/rollcontrol/a = [-kd/Izz 0; 1 0];
b = [lf/Izz; 0];
c = [0 1];
d = 0;

sys_ss = ss(a,b,c,d,'statename',{'Angular Accel','Angular Vel'});

%Check it out
figure
pzmap(sys_ss)
title('Pole and Zero map of State Space Model')

figure
step(sys_ss)
title('Initial Step Response of State Space Equation')

%convert State Space to Laplace Transfer Function [num den] = ss2tf(a,b,c,d);

%create root locus plot
figure
rlocus(num,den)
title('Continuous Initial Root locus')

%Create proportional controller

s = tf('s');

Gp = tf(num,den) | %Gp is the system process
kp = .000153; | %proportional gain chosen from rl graph
Gc = kp; | %Gc is the Controller process
cltf = feedback(Gc*Gp,1); | %closed loop response

figure

step(cltf)
title('Continuous system with kp')

%Now add a derivitive gain to speed things up

figure
rlocus(Gc*Gp)
title('Continuous system kp Root Locus')
kd = 100; | %derivitave gain
Gc = kp+kd*s | %new controller process
cltf = feedback(Gc*Gp,1) | %new closed loop response

figure
step(cltf)
title('Continuous system PD controller Step Response')

figure
impulse(cltf)
title('Continuous system PD controller Impulse Response')

%{
No Integrator required
Sys is arleady type 2,
steady state error goes to zero
if integrator is added the sys blows up
%}

%now model as discrete time and hope we can get close to the continuous

Ts = .01; | %sample time of 10 ms chosen. %Not sure what the actual sensors can do

z = tf('z',Ts);

sysd = c2d(Gp,Ts,'zoh') | %convert continous to discrete

figure
rlocus(sysd)
title('Initial Discrete System Root locus')
kp = .000153; | %new proportional gain chosen from rl graph
Gc = kp; | %new controller process
cltf = feedback(Gc*sysd,1) | %new closed loop response

figure

step(cltf)
title('Discrete system P controller Step Response')

%Now add a derivitive gain to speed things up

figure
rlocus(Gc*sysd)
title('Discrete system kp Root Locus')
kd = 1000; | %new derivative gain chosen from rl graph %acceptable values are 100-9000 %they depened on the systems capabilities %larger value = faster rise time
Gc = kp+kd*((z-1)/z) | %new controller process
cltf = feedback(Gc*sysd,1) | %new closed loop response

figure
step(cltf)
title('Discrete system PD controller Step Response')

figure
impulse(cltf)
title('Discrete system PD controller Impulse Response')

final_gp = d2c(sysd,'tustin')
final_gc = d2c(Gc,'tustin')

Gp =

0.8867
s^2 + 0.02327 s

Continuous-time transfer function.

Gc =

100 s + 0.000153

Continuous-time transfer function.

cltf =

88.67 s + 0.0001357
s^2 + 88.69 s + 0.0001357

Continuous-time transfer function.

sysd =

4.433e-05 z + 4.433e-05
z^2 - 2 z + 0.9998

Sample time: 0.01 seconds
Discrete-time transfer function.

cltf =

6.782e-09 z + 6.782e-09
z^2 - 2 z + 0.9998

Sample time: 0.01 seconds
Discrete-time transfer function.

Gc =

1000 z - 1000
z

Sample time: 0.01 seconds
Discrete-time transfer function.

cltf =

0.04433 z^2 - 3.432e-06 z - 0.04433 -----------------------------------z^3 - 1.955 z^2 + z - 0.04433

Sample time: 0.01 seconds
Discrete-time transfer function.

final_gp =

-8.598e-10 s^2 - 0.004433 s + 0.8867 ------------------------------------s^2 + 0.02327 s + 9.947e-14

Continuous-time transfer function.

final_gc =

2000 s + 0.0306

s + 200

Continuous-time transfer function.

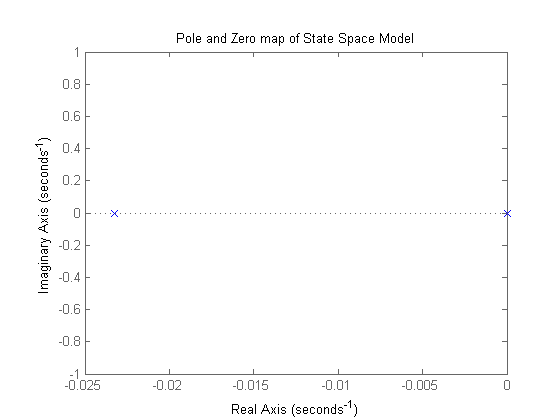
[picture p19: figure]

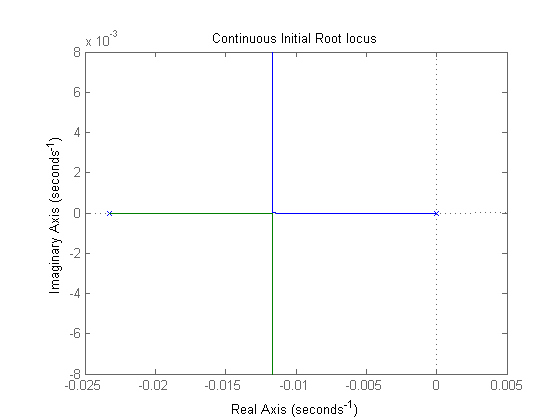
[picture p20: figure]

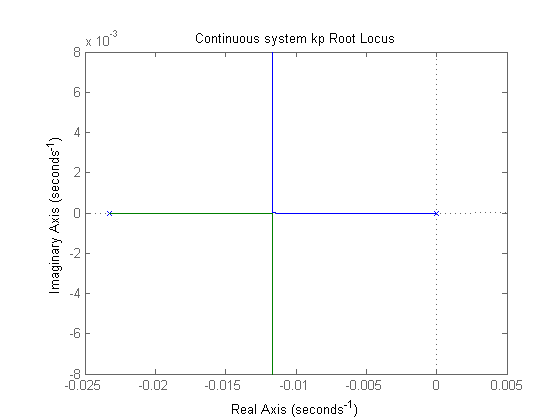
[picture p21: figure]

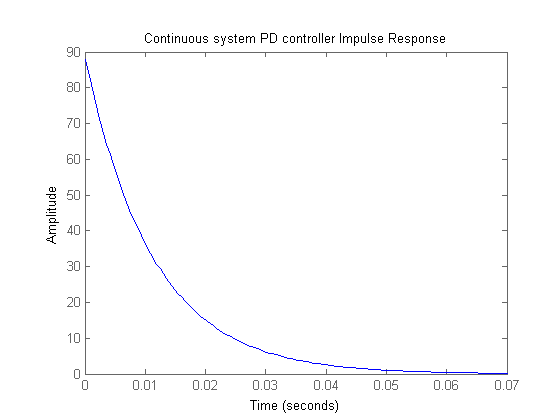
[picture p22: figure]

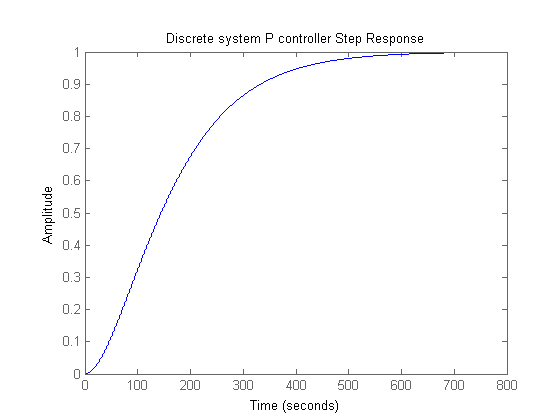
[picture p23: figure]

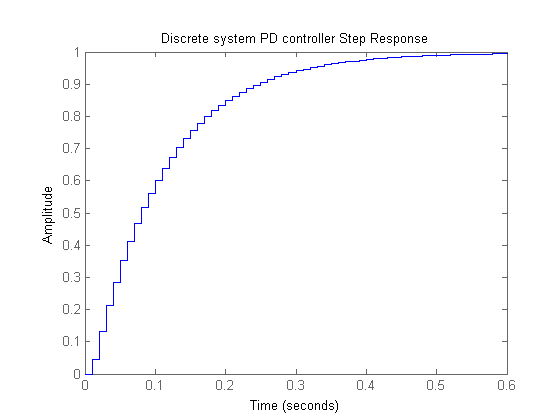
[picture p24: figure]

Published with MATLAB® R2013b

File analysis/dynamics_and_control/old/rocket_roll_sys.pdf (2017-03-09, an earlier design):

close all
clear

%import all trial data and split the runs and time start at zero

data = importdata('data.txt');
state0 = data(:,1);
state0 = state0(8:end);
time0 = data(:,3);
time0 = time0(8:end);
time0 = time0 - time0(1);
vel0 = data(:,2)*-1;
vel0 = vel0(8:end);

data = importdata('impulse1.txt'); state1 = data(:,1);
time1 = data(:,3);
vel1 = data(:,2);

state11 = state1(8:2924);
time11 = time1(8:2924);
time11 = time11 - time11(1); vel11 = vel1(8:2924)*-1;

%Graph all the collected data
figure
plot(time0,vel0,time0,state0) legend('Velocity (rad/s)','Duty Cycle State') title('Impulse Data')
xlim([0 .25])

figure
plot(time11,vel11,time11,state11) legend('Velocity (rad/s)','Duty Cycle State') title('Impulse Data 11')
xlim([0 .25])

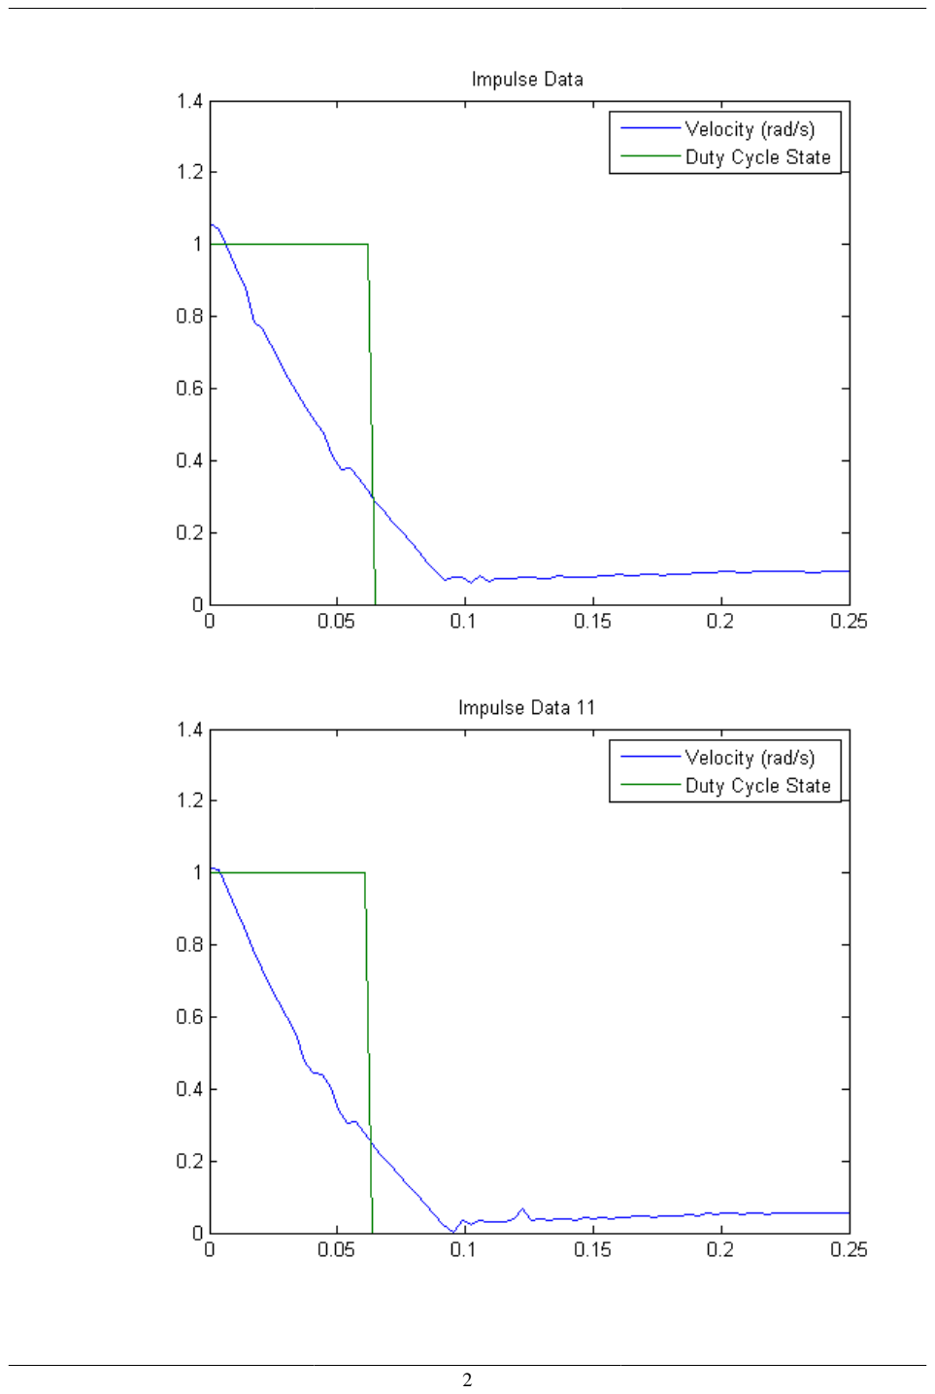
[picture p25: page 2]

%define model variables
I = 0.0198;
Ftot = 11;
fr = 2.75*.0254;
b = 0.002;
a = 2; %I/(Ftot*ct*fr)
Tau = 0.02;
hz = 10;

simout = sim('rocket_roll_sim.slx');

figure
plot(theta_dot.time,theta_dot.signals.values)
title('Step response of Theta Dot (rad/s)')

figure
plot(error.time,error.signals.values,time0,vel0,time11,vel11) legend('Simulation','Experimental 1','Experimental 2') title('Disturbance Rejection of Error (rad/s)')
xlim([0 .25])


Published with MATLAB® R2013b

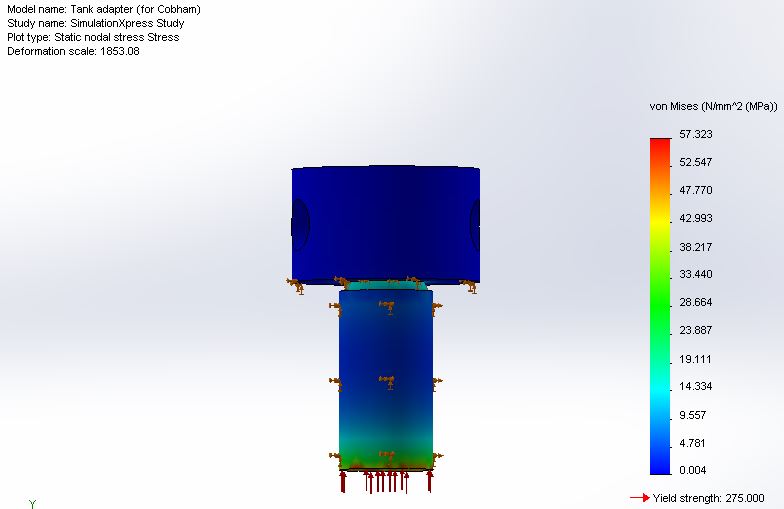
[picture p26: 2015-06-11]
cad/sw-cad-RCS_Module_LV3.0/Solid Model Renders/tank adapter FEA.JPG

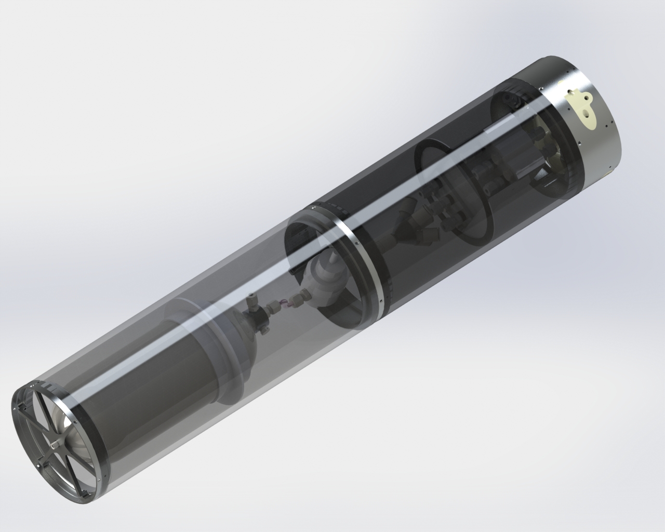
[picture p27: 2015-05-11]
cad/sw-cad-RCS_Module_LV3.0/Solid Model Renders/full system2.JPG

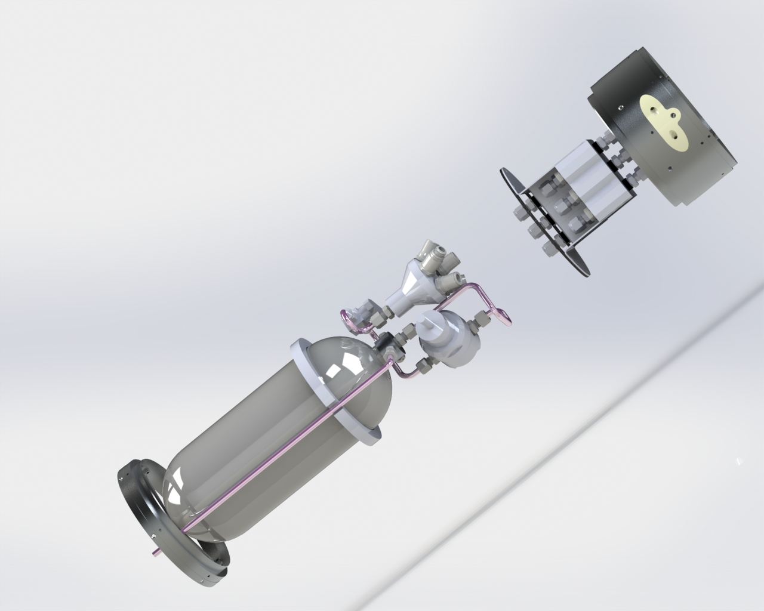
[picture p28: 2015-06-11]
cad/sw-cad-RCS_Module_LV3.0/Solid Model Renders/RCS Full Final.JPG

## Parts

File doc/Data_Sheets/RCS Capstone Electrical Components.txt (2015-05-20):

RCS Capstone Electrical Components

Pressure transducer 
Datasheet link ---- https://drive.google.com/open?id=0By5gRimJqF9NN0Vka1hUYUhEWFE&authuser=1
Quantity = 1
Manufacturer Ashcroft
Part# G2 M01 15 F2 5000# 
input voltage: 9-36Vdc
output voltage: 1-5Vdc
supply current 4: mA

Purpose
The pressure transducer will be used to measure remaining mass of N2 during flight for delta v calculations.

Time Sampling 
Sample rate should be no less than 10 Hz

Data Transferred
The pressure transducer will output a voltage that needs to be interpreted as the pressure remaining in the tank

Connections
There are four wires inside a shielded cable.  Red and Black are for input voltage and White and grey for output.	
System Location
The pressure transducer is located at the nozzle of the gas tank and has a 2 ft cable.

Solenoids 
Datasheet link ------ https://drive.google.com/open?id=0B8UrrhXeCpzyRVZVd2dITTNTVDg&authuser=1
Quantity: 6
Model# 320
Manufacturer: Humprey
Electrical Specs
Voltage: 24V DC w/ range of +10% and -15%
Resistance: 72 Ohms
Current: 333mA
Power Consumption: 8 W max draw 
Response time: on - 0.018 s, off - 0.009 s

Purpose
The solenoids will be actuated to a given range of duty cycle by the rocket’s computer using a control algorithm. 
Temperatures
Ambient temperature range: 32 F to 125 F

Connections
There are two 24 in black lead wires 18 AWG.
Humphry spec sheet on the 3rd page mentions two different connectors that can be ordered.

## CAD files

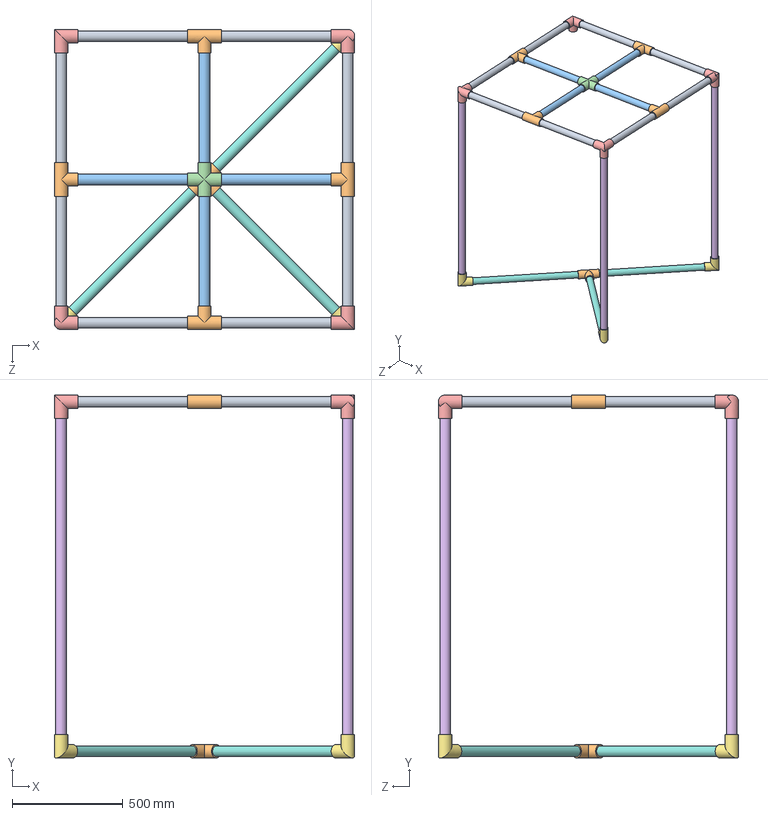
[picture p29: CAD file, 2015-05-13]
RCS inverted pendulum test stand/RCS inverted pendulum stand.SLDASM
1357.0 x 1639.6 x 1356.4 mm
1_5PVC4ft x 4
1_5PVC Tee x 5
1_5PVC23in x 4
1_5PVC cross
1_5PVC 3way90deg x 4
1_5PVC5ft x 3
1_5PVC90deg 2 x 3
1_5PVC34in x 3

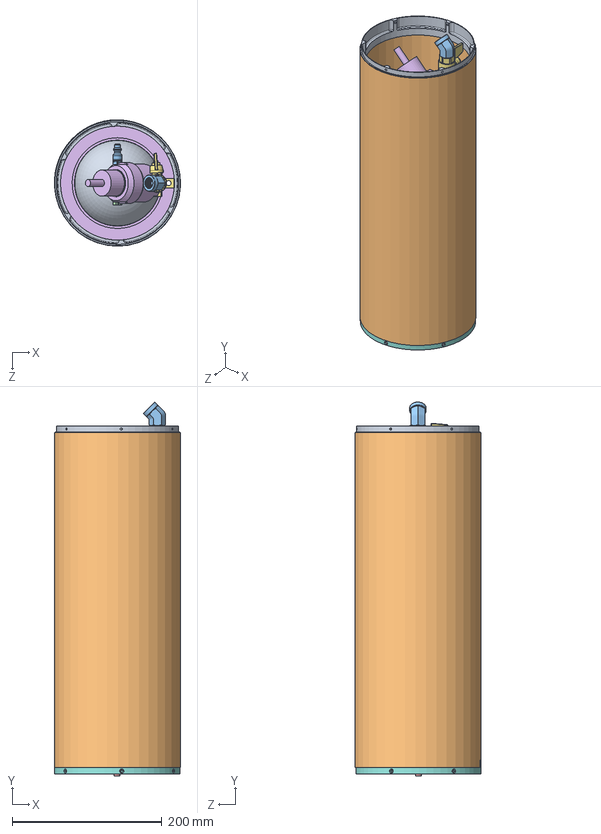
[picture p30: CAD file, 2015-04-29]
sw-cad-RCS_Module_LV3.0/Tank Module Assembly/Tank Module Assembly.SLDASM
168.6 x 499.9 x 169.0 mm
Air_Tank (Luxfer L17D 150ci)
Tank adapter (for Luxfer)
.125 NPT quick disconnect
Burst disc x 2
HP_Gauge
Swagelock Regulator
4082T420
FCR 6in 4_6_14 Final
MCR 6in 4_6_14 Final
Carbon Sleeve
48805K183 x 3
Tank brace
90860A113
Tank Centering ring
regulator mount

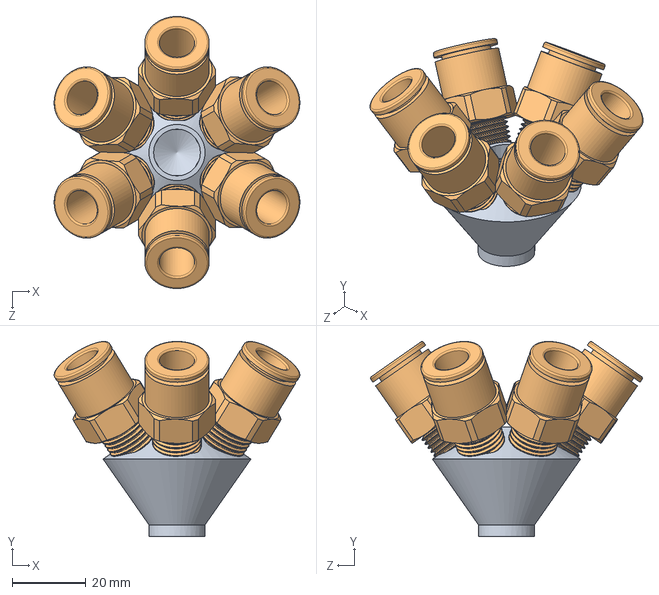
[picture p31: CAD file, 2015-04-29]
cad/sw-cad-RCS_Module_LV3.0/Manifold Ideas/6in0 assembly.SLDASM
66.7 x 52.9 x 73.8 mm
manifold 6 surround 0 center one piece
5526K730 x 6

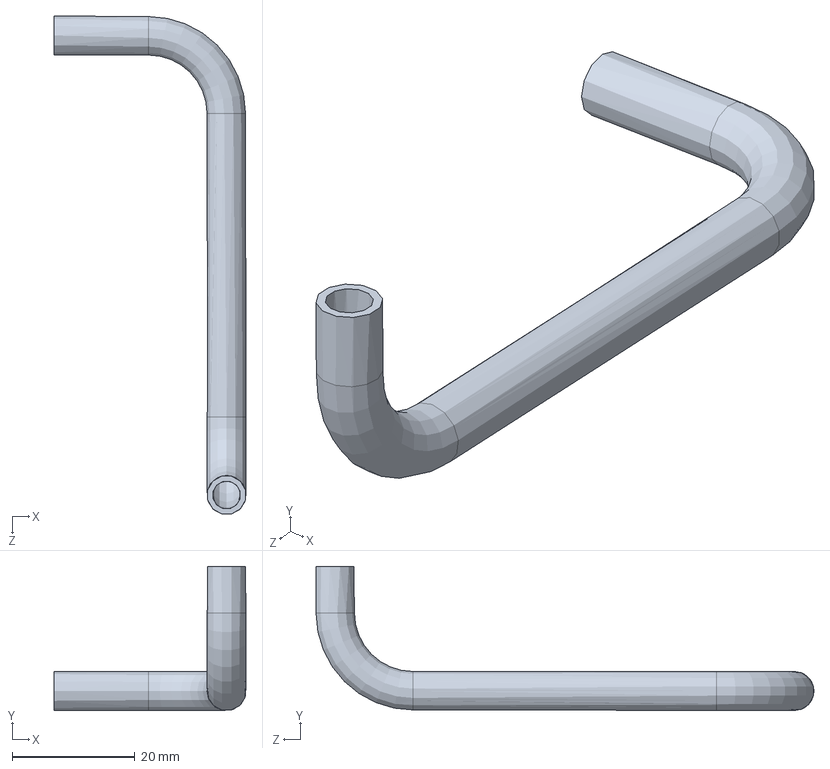
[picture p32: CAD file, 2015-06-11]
cad/sw-cad-RCS_Module_LV3.0/Tank Module Assembly/Tube_11-Tank Module Assembly.sldasm
31.2 x 23.4 x 81.0 mm

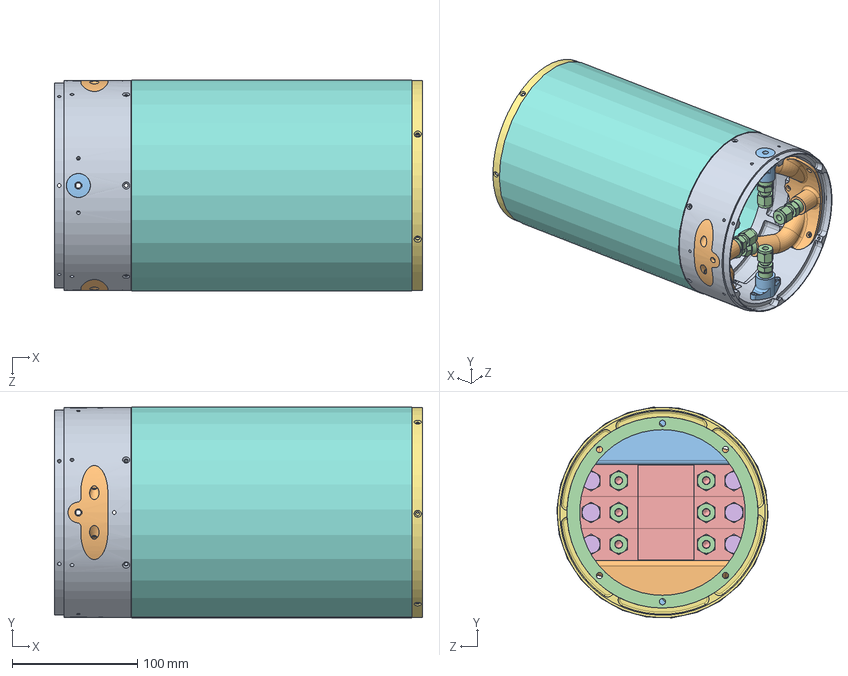
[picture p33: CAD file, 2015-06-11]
cad/sw-cad-RCS_Module_LV3.0/nozzle ring v2/nozzle ring v2.SLDASM
293.5 x 168.0 x 168.6 mm
Nozzle carrying ring (3_4_15)
deLaval roll and pitch coupled nozzles x 2
deLaval pitch yaw x 2
straight fitting x 20
solenoid (humphrey 320) x 6
.25 NPT Plug x 6
FCR 6in Final
Fiberglass nozzle module Sleeve
MCR 6in Final
Solenoid bracket (right)
Solenoid bracket (left)
solenoid attachment ring

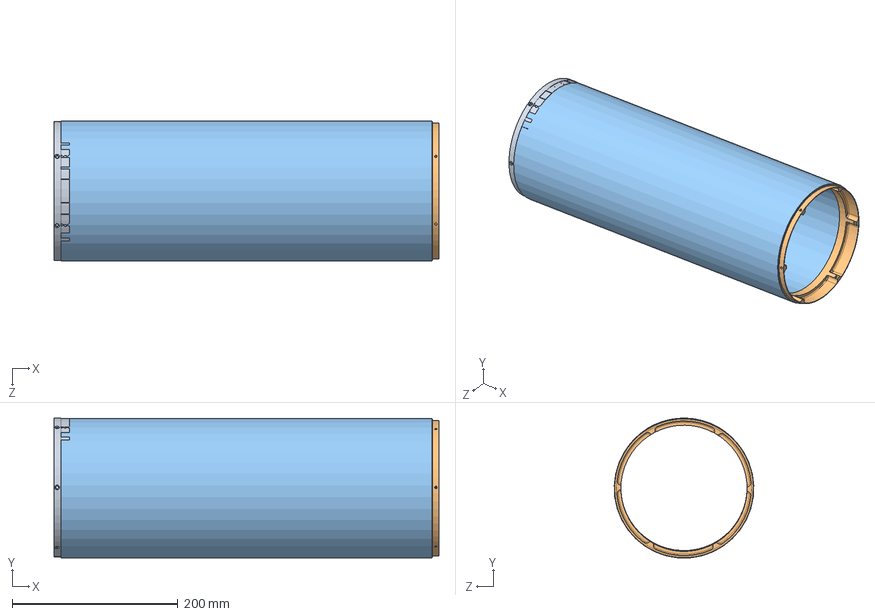
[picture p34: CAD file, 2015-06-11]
cad/sw-cad-RCS_Module_LV3.0/Tank Module Assembly/Module_ASSY.SLDASM
464.8 x 168.9 x 168.6 mm
FCR 6in 4_6_14 Final
MCR 6in 4_6_14 Final
Carbon Sleeve

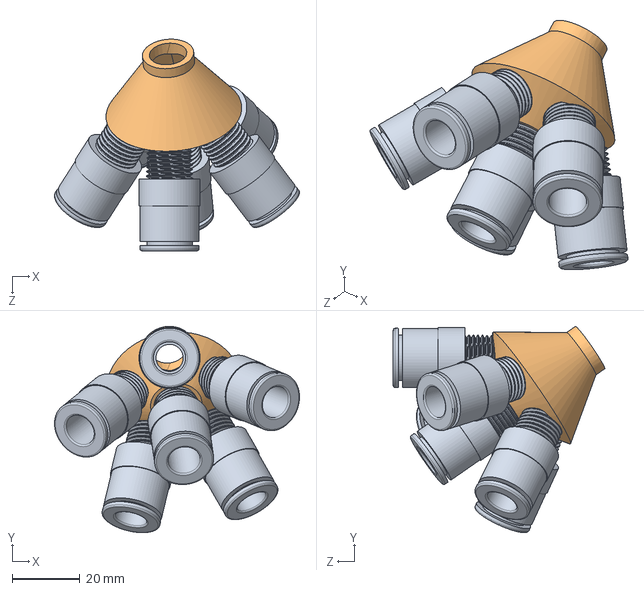
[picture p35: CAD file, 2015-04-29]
cad/sw-cad-RCS_Module_LV3.0/Manifold Ideas/5in1 assembly.SLDASM
72.3 x 60.9 x 62.4 mm
5526K730 x 6
manifold 5 surround 1 center one piece

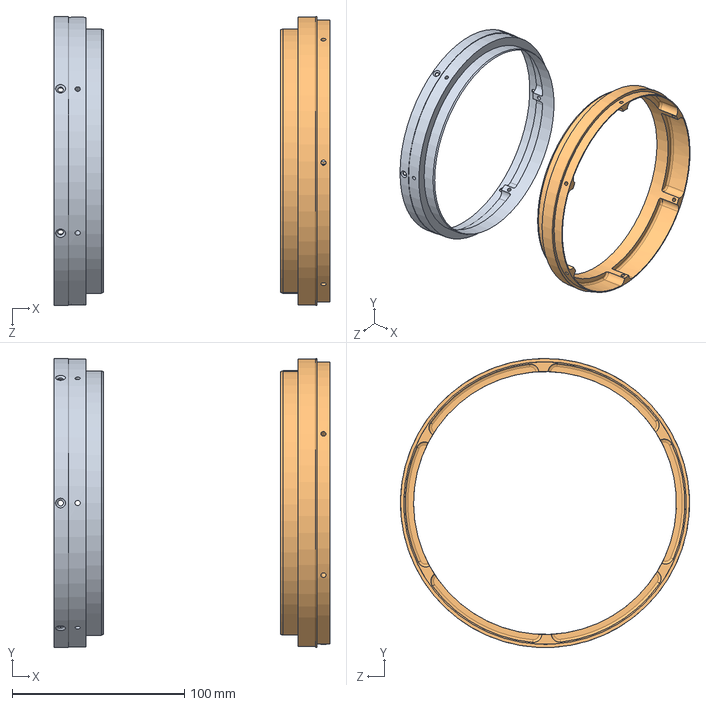
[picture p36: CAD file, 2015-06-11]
cad/sw-cad-RCS_Module_LV3.0/nozzle ring v2/Short Module.SLDASM
160.0 x 167.6 x 167.6 mm
FCR 6in Final
MCR 6in Final

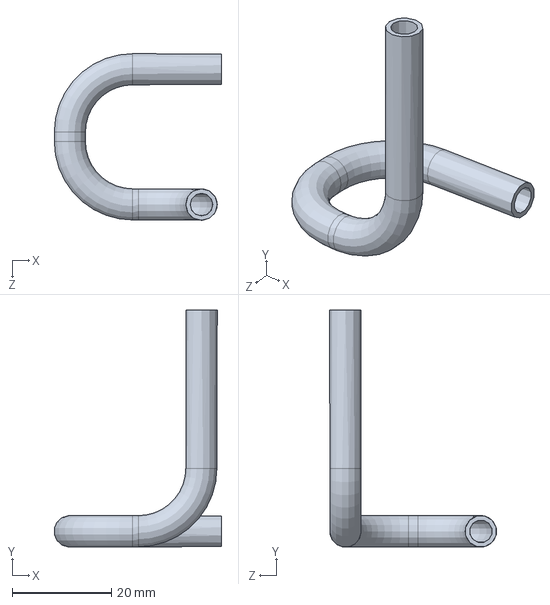
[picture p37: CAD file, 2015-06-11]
cad/sw-cad-RCS_Module_LV3.0/Tank Module Assembly/Tube_12-Tank Module Assembly.sldasm
33.7 x 47.8 x 33.6 mm

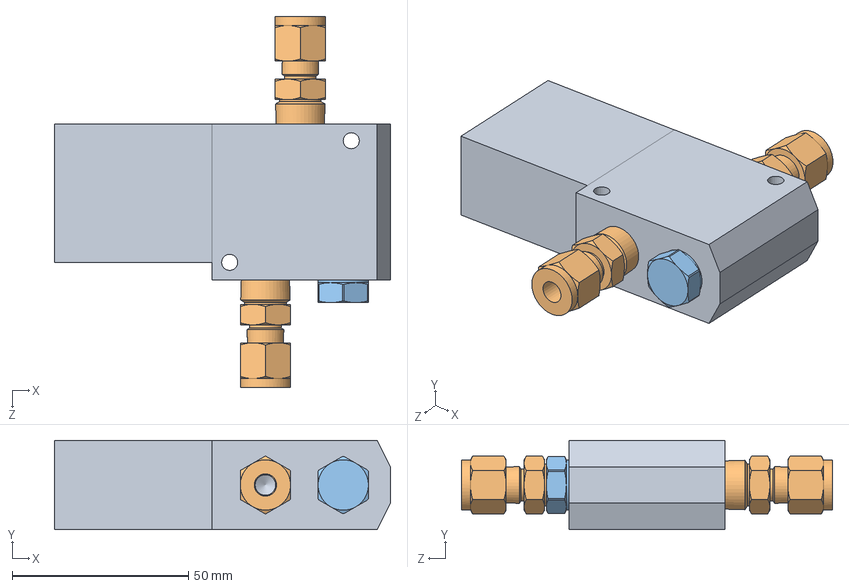
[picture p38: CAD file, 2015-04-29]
cad/sw-cad-RCS_Module_LV3.0/nozzle ring v2/solenoid with fittings.SLDASM
95.5 x 25.4 x 105.4 mm
solenoid (humphrey 320)
straight fitting x 2
.25 NPT Plug

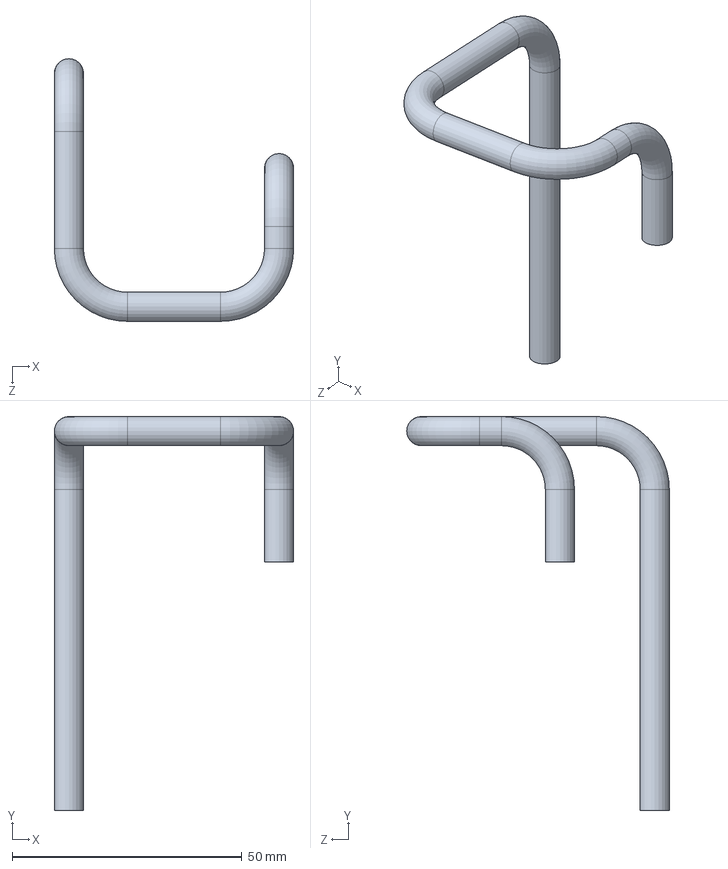
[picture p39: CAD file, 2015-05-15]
cad/sw-cad-RCS_Module_LV3.0/Tank Module Assembly/Tube_3-Tank Module Assembly.sldasm
52.1 x 85.7 x 57.2 mm

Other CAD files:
cad/sw-cad-RCS_Module_LV3.0/Tank Module Assembly/Tube_4-Tank Module Assembly.sldasm
cad/sw-cad-RCS_Module_LV3.0/Tank Module Assembly/Tube_13-Tank Module Assembly.sldasm
cad/sw-cad-RCS_Module_LV3.0/Tank Module Assembly/Tube_6-Tank Module Assembly.sldasm
cad/sw-cad-RCS_Module_LV3.0/Tank Module Assembly/Tube_2-Tank Module Assembly.sldasm
cad/sw-cad-RCS_Module_LV3.0/Tank Module Assembly/Tube_9-Tank Module Assembly.sldasm
cad/sw-cad-RCS_Module_LV3.0/nozzle ring v2/Tube_1-solenoid with fittings-001.sldasm
cad/sw-cad-RCS_Module_LV3.0/nozzle ring v2/Tube_1-nozzle ring v2.sldasm
cad/Supporting_CAD/Nozzles/Test Nozzles/Test Nozzle Rev 0/RCS_nozzle.SLDDRW
cad/Supporting_CAD/Nozzles/Test Nozzles/Test Nozzle Rev 0/RCS_nozzle.SLDPRT
cad/Supporting_CAD/Nozzles/Test Nozzles/deLaval cutaway.SLDPRT
cad/Supporting_CAD/Nozzles/Test Nozzles/deLaval.SLDPRT
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

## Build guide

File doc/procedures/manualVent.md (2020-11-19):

# Venting Procedure
## Notes
- The vent system definitely needs a choke, and probably a rudimentary diffuser.
    - The choke would limit the rate of discharge.
        - This would reduce damage from any FOD, thrust during venting, and limit expansion cooling to the choke.
        - It might be a good idea to put a cold sink on the choke.
        - During testing, we would defninitely want to monitor the temperature of the choke.
    - The diffuser would minimize the thrust produced by the venting procedure.
- On the vent system, we may want to add a pressure gauge between the coupling and the choke.

## Nomenclature
- "Caution" = potential damage to equipment
- "Danger" = potential damage to people (and potentially equipment).
- "FOD" = Foreign Object Debris (anything that shouldn't be there, e.g., dirt, metal shavings, grease, water, stray tools)
- "PPE" = Personal Protective Equipment
- "NOID" = NO IDentifier
    - Anything marked with NOID needs an identifier in the procedure and system-level illustration.

## Required Materials
| Quantity | Part Name | Identifier | Part Number
| --- | --- | --- | ---
| 1 | Reaction Control System |  |  
| 1 | RCS Venting System |  |  
| 1 | impact-resistant safety goggles (TODO: ANSI standard) |  |  
| 1 | heavy hearing protection (TODO: ANSI standard) |  |  
| 1 | dry cloth |  |  
| 1 |  |  |  
| 1 |  |  |  

## General Precautions
- The internal components of the RCS and its venting system are sensitive to FOD.
    - It's important to keep work areas clean to avoid contamination.
- The RCS is nominally pressurized to 238 atmospheres and stores an equivalent energy of 27.1 g TNT.
    - This is enough to (TODO: look up medical hazards) and eject FOD/shrapnel.
    - People must wear the above-listed PPE when within (TODO: safe radius) of the RCS when it is pressurized.

## Operations
### Preparation
1. Preparing the vent system:
    1. Ensure `BV-VTA` is closed. (TODO: orientation?)
    1. Ensure `NV-01` is closed. (TODO: orientation/instructions?)
    1. Remove the dust covers on both ends of the vent system.
    1. Ensure both ends are free of FOD. (TODO: cleaning procedure)
- Danger: 
    - When pressurized the RCS stores energy equivalent to (TODO: better calculation than naive pressure x volume) 27.1 g of TNT. (safe radius (TODO) ?? m)
    - Anyone within (TODO) SAFE RADIUS must wear (TODO) REQUIRED PPE:
        - Impact-resistant safety goggles. (TODO: ANSI standard)
1. Preparing the RCS system:
    1. Remove the dust cover from `HC-01`.
    1. Ensure `HC-01` is free of FOD. (TODO: cleaning procedure)
- Danger: 
    - Once the vent system is attached, it will be pressurized.
    - If `BV-VTA` is not closed, it may act like a thruster.
1. Attaching the vent system to the RCS:
    1. Couple `HC-02` to `HC-01` such that there is an audible click. (TODO: update labels)
    1. Tug gently on `HC-02` to confirm the connection.
    1. Ensure the outlet(s) of the vent system (NOID), are not facing any people.

### Venting Proper
1. Ensure the outlet(s) of the vent system (NOID), are not facing any people.
- Danger: 
    - If `NV-01` is not closed by the next step, the vent system may act like a thruster.
    - If the vent system contains FOD, the FOD may be violently discharged and/or damage internal components.
2. Open `BV-VTA`. (TODO: orientation)
3. Open `NV-01` slowly until a moderate hissing noise is heard. (TODO: direction/instructions, number of turns)
4. Retreat beyond (TODO) SAFE RADIUS from the RCS.
5. Wait for the hissing noise to stop.
6. Approach the RCS.
7. Repeat steps 2 through 5 of the "Venting Proper" procedure until `NV-01` is fully open and no hissing is heard.

### Tidying Up
1. Ensure the down-stream-end of the venting system and its dust cover are free of FOD. (TODO: cleaning procedure)
1. Cover the down-stream end of the venting system with its dust cover.
1. Close `HV-VTA`. (TODO: orientation)
1. Close `NV-01`. (TODO: direction/instructions)
1. If `HC-01` and `HC-01` covered in ice, wait for it to thaw and wipe off the moisture. 
   (NOID: the sides of the couplings need separate identifiers)
1. Ensure the dust covers for `HC-01` and `HC-01` are free of FOD. (NOID)
- Danger: 
    - If pressure remains in the system, the next step may eject `HC-01` and/or any FOD present.
1. Decouple `HC-01` from `HC-01`.
1. Ensure `HC-01` and `HC-01` are free of FOD. (TODO: cleaning instructions)
1. Replace the dust covers on `HC-01` and `HC-01`.

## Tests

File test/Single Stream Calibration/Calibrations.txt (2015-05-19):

High Pressure:

1333.1735*V(transducer)-1324

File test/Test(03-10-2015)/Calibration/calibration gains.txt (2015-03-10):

calibration gain:
 
Force: -.095 ish  (gain 100)
pressure: .996 ish (gain 1)
Temperature: gain 100

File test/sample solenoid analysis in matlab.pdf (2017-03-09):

close all;
clear;

load('matlab 200ms 50 duty.mat');

figure
plot(time,VoltageSolenoid,time,LoadcellVoltage) title('Unfiltered Data')

Solenoid = VoltageSolenoid(2:end);
LoadCell = LoadcellVoltage(2:end);
time = time(2:end);

%{

Sole = fft(VoltageSolenoid); Load = fft(LoadcellVoltage);

figure
hold on
plot(time,Sole,time,Load)
legend('Sole','Load')
title('Filtered Data')
hold off
%}

%
%best fc for butterworth
%Using Residual Analysis

%unblock to see graph for determining fc fs=1000; %sampling frequency
fc= 1:.1:100;
n=7; %number of series

for i=1:length(fc)
| [b,a] = butter(n,fc(i)/(fs/2),'low'); y= filter(b,a,LoadCell); res(i)=sqrt(sum((LoadCell-y).^2)/length(y)); i=i+1;

end

figure
plot(fc,res)
title('Residuals Plot')
grid on

%implement lowpass butterworth filter for 1000hz

fc=50; %cutoff frequency

[b,a] = butter(n,fc/(fs/2),'low'); LoadCell = filter(b,a,LoadCell); Solenoid = filter(b,a,Solenoid);

figure
hold on
plot(time,Solenoid,time,LoadCell) legend('Solenoid','LoadCell') title('Filtered Data')
hold off

%LoadCell = (207.56*LoadCell-0.656)*-1; Solenoid = Solenoid*-1+.8;

figure
plot(time,Solenoid,time,LoadCell) legend('Solenoid','LoadCell') title('Filtered Data')

%find peaks(ampl) to analyze freq and period %findpeaks returns sequence, not time vaule [pks_l,loc_l]=findpeaks(LoadCell,'minpeakheight',.035); [pks_s,loc_s]=findpeaks(Solenoid,'minpeakheight',.8);

%invert the data to find the valleys
LoadCell_inv = 1.01*max(LoadCell) - LoadCell;
Solenoid_inv = 1.01*max(Solenoid) - Solenoid;

[pks_l_inv,loc_l_inv]=findpeaks(LoadCell_inv);%,'minpeakheight',.035); [pks_s_inv,loc_s_inv]=findpeaks(Solenoid_inv);%,'minpeakheight',.8);

pks_l_inv = LoadCell(loc_l_inv);
pks_s_inv = Solenoid(loc_s_inv);

figure
hold on
plot(time,LoadCell,time,Solenoid) scatter(time(loc_l),pks_l) scatter(time(loc_s),pks_s) scatter(time(loc_l_inv),pks_l_inv) scatter(time(loc_s_inv),pks_s_inv)
title('Lowpass Butterworth Filter with Optimal Fc') legend('Load cell Voltage','Solenoid Voltage')

%Analyze only first three complete cycles
loc_s = loc_s([2 6 7 11 12 16]);
pks_s = pks_s([2 6 7 11 12 16]);

loc_l = loc_l([1 3 4 6 7 10]);
pks_l = pks_l([1 3 4 6 7 10]);

pks_l_inv = [pks_l_inv([4 7]);LoadCell(280);pks_l_inv([13 17 21])]; loc_l_inv = [loc_l_inv([4 7]);280;loc_l_inv([13 17 21])];

pks_s_inv = pks_s_inv([2 7 11 16 20 25]);
loc_s_inv = loc_s_inv([2 7 11 16 20 25]);

time = time(1:600);
LoadCell = LoadCell(1:length(time)); Solenoid = Solenoid(1:length(time));

figure
hold on
plot(time,LoadCell,time,Solenoid) scatter(time(loc_l),pks_l) scatter(time(loc_s),pks_s) scatter(time(loc_l_inv),pks_l_inv) scatter(time(loc_s_inv),pks_s_inv)
%title('Lowpass Butterworth Filter with Optimal Fc') legend('Load cell Voltage','Solenoid Voltage') xlabel('Time (s)')
ylabel('Voltage (V)')
grid on
grid minor

time(loc_l)
time(loc_s)

total_time_loadcell_on_off = diff(time(loc_l_inv)) total_time_solenoid_on_off = diff(time(loc_s_inv))

fully_developed_loadcell_on_off = diff(time(loc_l)) fully_developed_solenoid_on_off = diff(time(loc_s))

%}

%{
%find valleys?
[Maxima,MaxIdx] = findpeaks(Data); DataInv = 1.01*max(Data) - Data; [Minima,MinIdx] = findpeaks(DataInv); Minima = Data(MinIdx);
%}

ans =

0.1010
0.1580
0.3000
0.3610
0.5010

0.5640

ans =

0.0710
0.1540
0.2720
0.3570
0.4720
0.5590

total_time_loadcell_on_off =

0.1110
0.0930
0.1090
0.0890
0.1090

total_time_solenoid_on_off =

0.1320
0.0680
0.1320
0.0680
0.1310

fully_developed_loadcell_on_off =

0.0570
0.1420
0.0610
0.1400
0.0630

fully_developed_solenoid_on_off =

0.0830
0.1180
0.0850
0.1150
0.0870

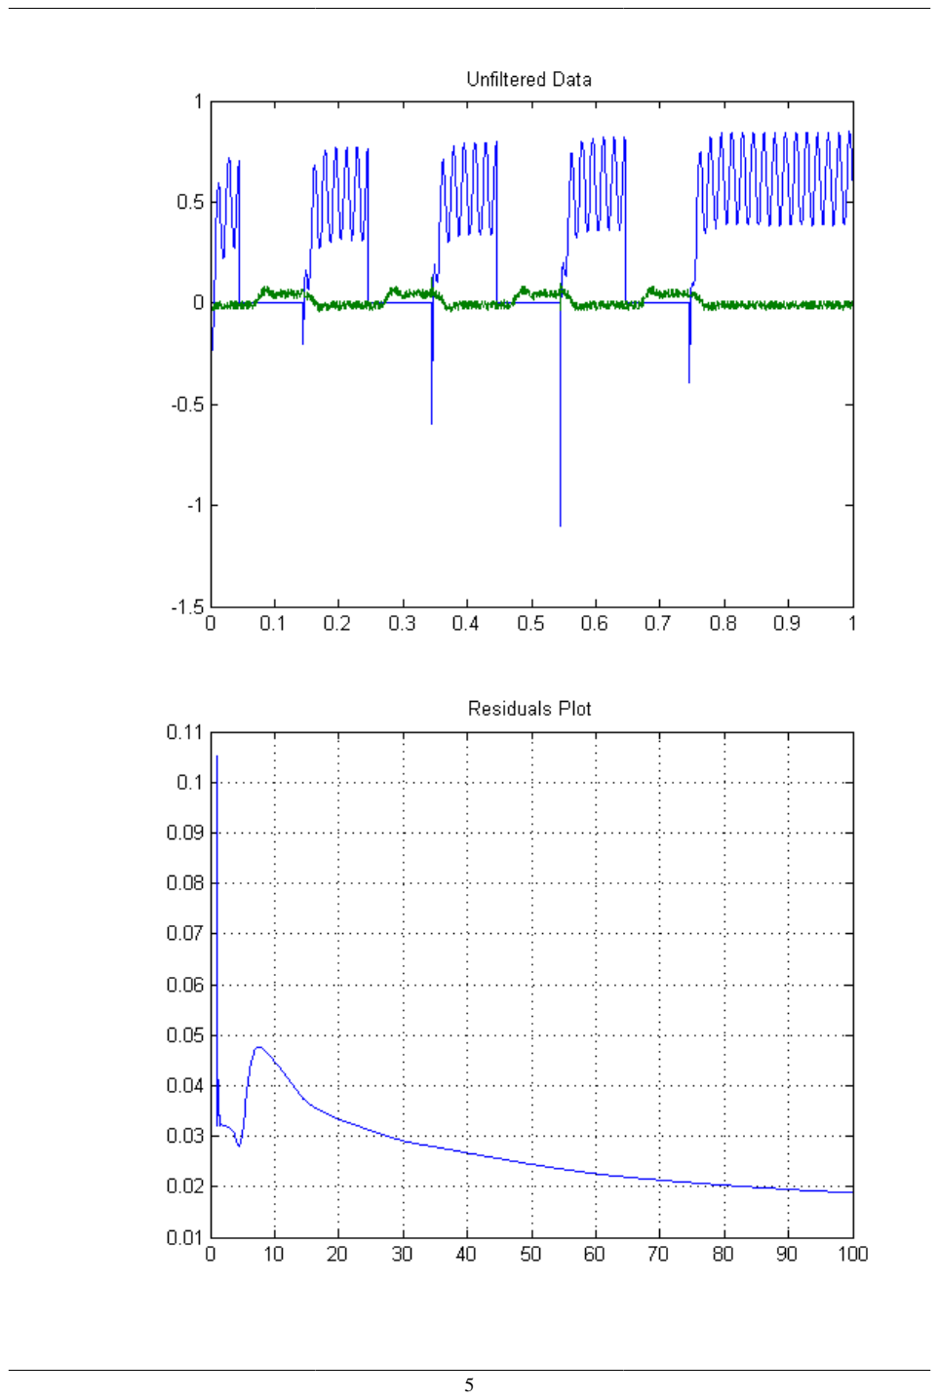
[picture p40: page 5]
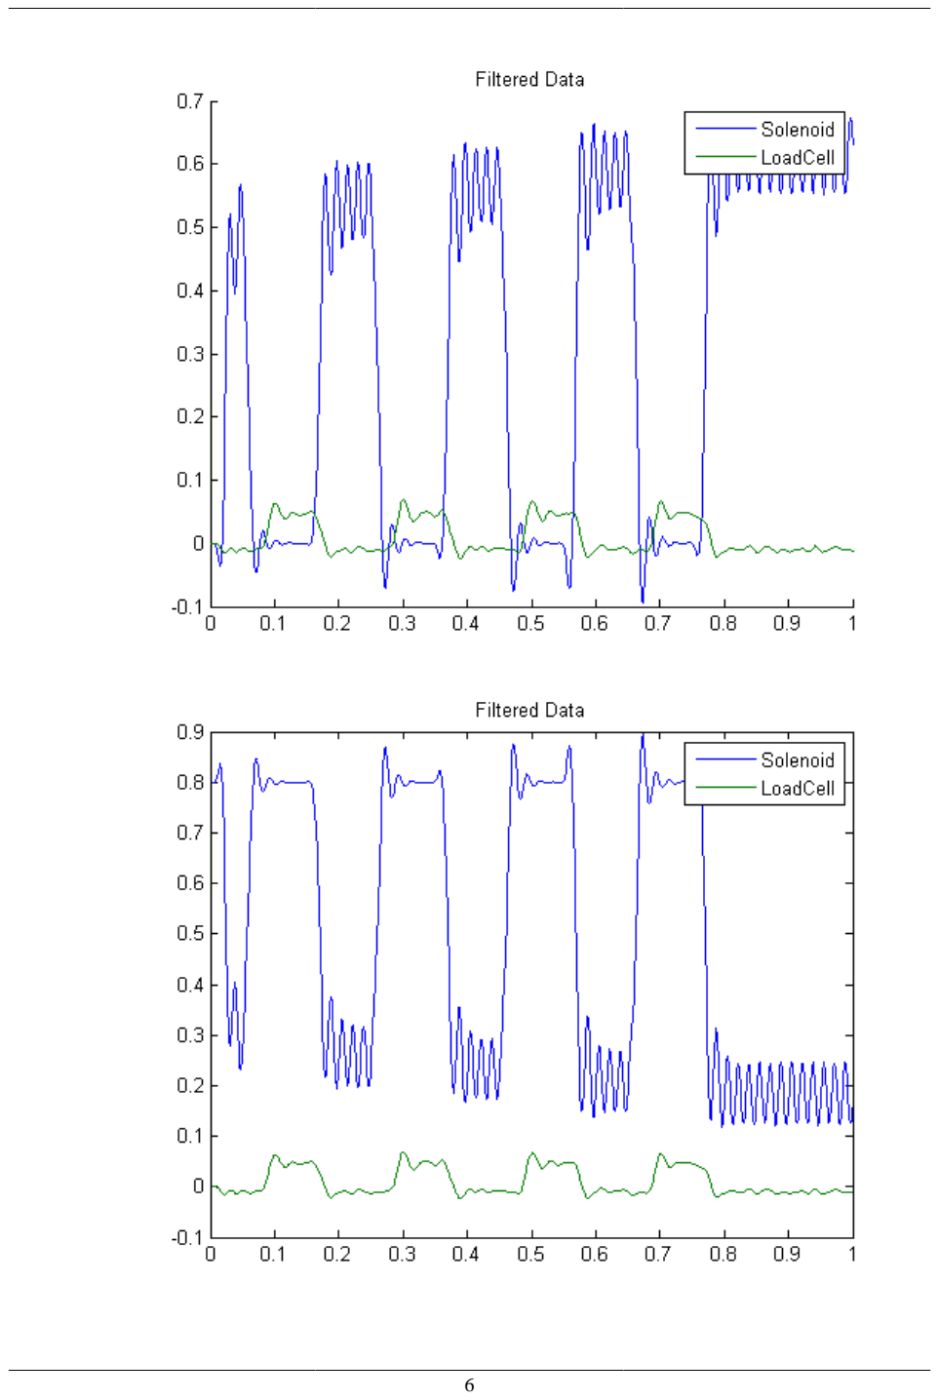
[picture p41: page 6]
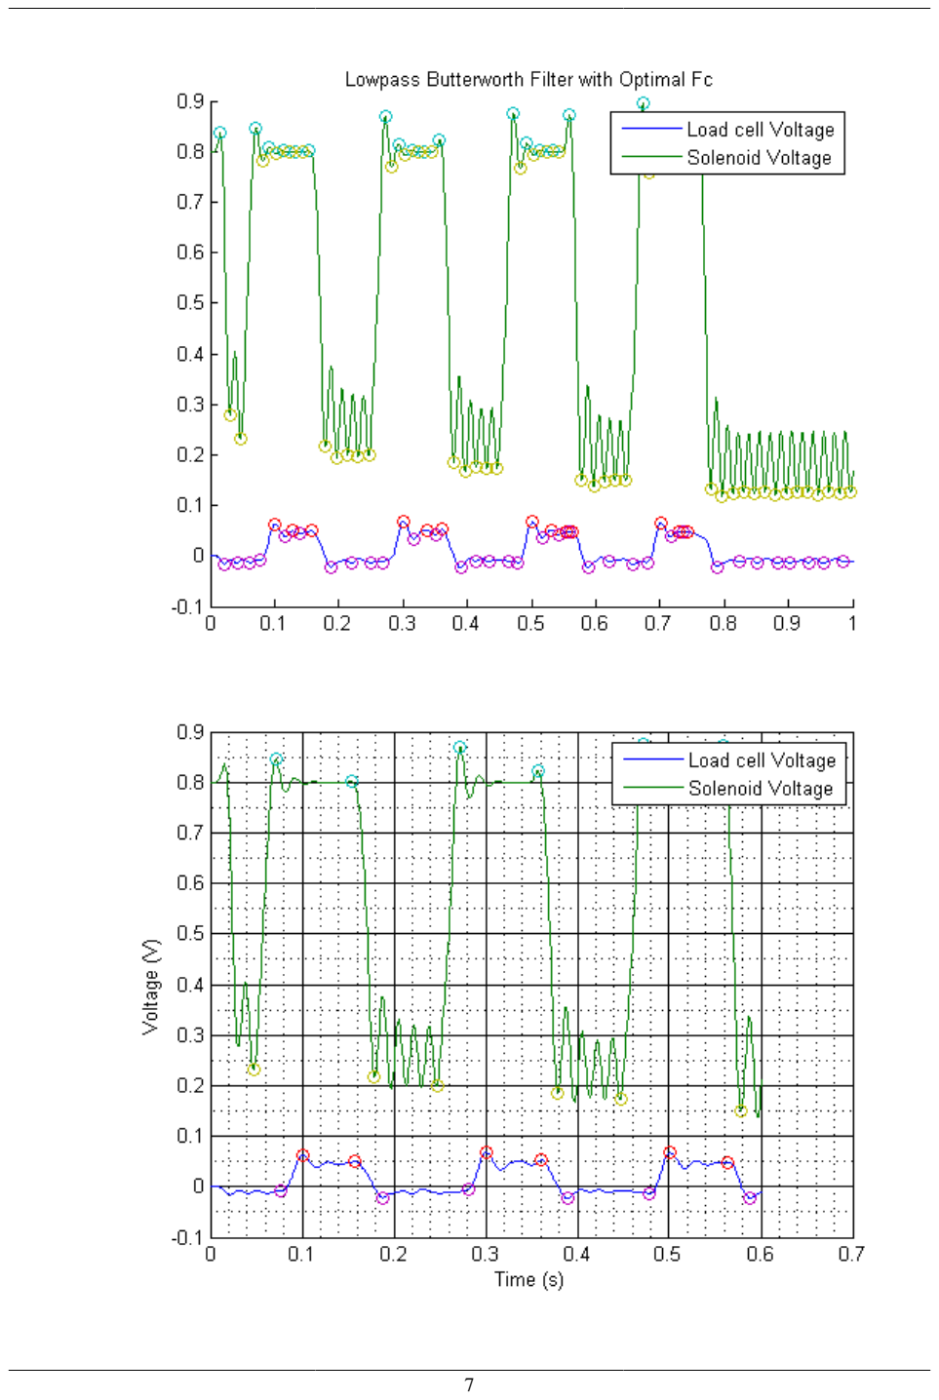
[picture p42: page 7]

Published with MATLAB® R2013a

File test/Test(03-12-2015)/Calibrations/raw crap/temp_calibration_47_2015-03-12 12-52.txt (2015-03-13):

temp_calibration2015-03-12 12-52.txt	
2015-03-12 12-52	
	
Temp (labview C)	time
43.099614	0
43.475786	0.003
43.475786	0.004001
43.601153	0.005001
42.974199	0.006001
42.095959	0.007001
43.601153	0.008001
42.597883	0.009002
42.346945	0.010002
42.723334	0.011002
42.597883	0.012002
42.597883	0.013002
42.974199	0.014003
43.726508	0.015003
42.974199	0.016003
42.974199	0.017003
42.974199	0.018003
43.099614	0.019004
43.475786	0.020004
43.851851	0.021004
43.977182	0.022004
43.475786	0.023005
42.095959	0.024004
41.970448	0.025005
42.597883	0.026005
43.099614	0.027005
42.47242	0.028006
42.974199	0.029006
42.346945	0.030006
42.848773	0.031006
41.844925	0.032006
41.970448	0.033007
42.974199	0.034007
42.848773	0.035007
43.350408	0.036007
43.099614	0.037007
43.601153	0.038007
43.350408	0.039008
42.723334	0.040008
42.597883	0.041008
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

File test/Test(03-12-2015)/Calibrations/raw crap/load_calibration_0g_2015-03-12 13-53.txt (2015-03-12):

load_calibration_0g_2015-03-12 13-53.txt
2015-03-12 13-53

Temp (labview C)	Loadcell Voltage	Voltage Solenoid	Voltage Pressure	time
24.654605	-0.006062	0.159015	-0.995534	0.000000
25.672678	0.018601	0.317514	-0.996192	0.003000
24.781914	0.021232	0.465162	-0.998494	0.004000
24.017850	0.002159	0.614783	-0.997178	0.005000
23.763048	-0.008364	0.796630	-0.996850	0.006000
24.527282	-0.010666	0.966639	-0.998165	0.007000
24.909208	0.007092	1.160653	-0.998494	0.008000
26.181377	0.002159	1.314878	-0.998494	0.009000
24.527282	-0.014940	1.441151	-0.997178	0.010000
25.418244	0.014655	1.540460	-0.996192	0.011000
24.399945	0.012682	1.580578	-0.996192	0.012000
23.635625	0.004461	1.597678	-0.996850	0.013000
25.036488	0.012682	1.544406	-0.997178	0.014000
24.399945	0.001501	1.481927	-0.996850	0.015000
24.527282	-0.013954	1.390182	-0.996521	0.016000
24.399945	0.012353	1.305670	-0.995863	0.017000
25.291006	-0.003431	1.244178	-0.998823	0.018000
24.145229	-0.017242	1.196825	-0.997178	0.019000
24.909208	0.007749	1.194523	-0.996850	0.020000
24.145229	0.020574	1.224776	-0.995205	0.021000
25.927056	-0.009350	1.294161	-0.997178	0.022000
24.017850	0.022547	1.396429	-0.997507	0.023000
24.781914	0.020574	1.505603	-0.996192	0.024000
24.145229	-0.011981	1.630562	-0.998494	0.025000
24.909208	0.013668	1.717375	-0.999809	0.026000
25.545468	0.011367	1.795967	-0.996521	0.027000
24.781914	-0.010994	1.837729	-0.998494	0.028000
24.527282	0.016299	1.832468	-0.995205	0.029000
24.017850	0.013340	1.803530	-0.998165	0.030000
24.654605	-0.014940	1.710798	-0.996192	0.031000
24.272594	0.018930	1.625629	-0.995534	0.032000
25.291006	-0.001458	1.500342	-0.996521	0.033000
24.781914	-0.015598	1.414187	-0.995205	0.034000
25.163754	0.005119	1.345460	-0.997836	0.035000
24.272594	0.011038	1.292846	-0.998494	0.036000
25.545468	-0.013954	1.293175	-0.995863	0.037000
23.890456	0.016628	1.316193	-0.995863	0.038000
24.909208	0.007749	1.402677	-0.996192	0.039000
25.291006	-0.007377	1.491135	-0.996521	0.040000
24.781914	0.020245	1.607543	-0.995534	0.041000
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

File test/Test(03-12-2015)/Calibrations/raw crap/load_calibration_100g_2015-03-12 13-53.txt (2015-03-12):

load_calibration_100g_2015-03-12 13-53.txt
2015-03-12 13-53

Temp (labview C)	Loadcell Voltage	Voltage Solenoid	Voltage Pressure	time
24.017850	0.009722	0.363223	-0.995863	0.000000
24.272594	-0.002116	0.581899	-0.994877	0.002000
24.145229	0.021889	0.762431	-0.997836	0.003000
25.799874	0.011038	0.939346	-0.995534	0.004000
24.527282	-0.006720	1.110341	-0.994877	0.005000
23.508189	0.023862	1.215569	-0.997836	0.006000
24.527282	-0.009021	1.279035	-0.996192	0.007000
24.017850	0.002159	1.283638	-0.997836	0.008000
24.527282	0.002488	1.256674	-0.996192	0.009000
25.163754	0.026493	1.204060	-0.997507	0.010000
24.781914	0.000844	1.136648	-0.997507	0.011000
25.163754	0.021232	1.094557	-0.996521	0.012000
23.635625	0.003474	1.071209	-0.997507	0.013000
24.145229	0.010709	1.066606	-0.996521	0.014000
25.927056	-0.010008	1.106724	-0.998494	0.015000
25.163754	0.020574	1.175780	-0.997178	0.016000
24.909208	0.017286	1.287255	-0.997178	0.017000
24.272594	-0.006062	1.399389	-0.996850	0.018000
25.418244	0.021232	1.539474	-0.995863	0.019000
23.763048	0.007092	1.640756	-0.997178	0.020000
24.781914	-0.008693	1.725924	-0.997507	0.021000
24.781914	0.026493	1.789061	-0.995534	0.022000
24.527282	0.010709	1.796625	-0.995534	0.023000
24.272594	-0.010337	1.783142	-0.997178	0.024000
25.545468	0.018272	1.702577	-0.996521	0.025000
23.763048	0.013668	1.623656	-0.996192	0.026000
24.399945	-0.011323	1.511523	-0.998494	0.027000
24.272594	0.015641	1.416489	-0.995534	0.028000
25.163754	0.019259	1.280021	-0.997178	0.029000
24.781914	0.027480	1.278048	-0.996850	0.030000
25.799874	0.022218	1.288242	-0.996521	0.031000
25.163754	0.003146	1.306657	-0.996192	0.032000
23.763048	-0.005733	1.374397	-0.994877	0.033000
24.272594	0.028795	1.467787	-0.996850	0.034000
24.654605	0.007092	1.573673	-0.996521	0.035000
24.272594	-0.009350	1.689424	-0.996850	0.036000
24.527282	0.021889	1.770975	-0.995534	0.037000
24.781914	0.017286	1.841018	-0.997178	0.038000
23.380738	0.000186	1.877190	-0.997178	0.039000
24.909208	0.023534	1.865680	-0.996521	0.040000
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

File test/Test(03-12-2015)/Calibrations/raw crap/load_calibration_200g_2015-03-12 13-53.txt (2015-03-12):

load_calibration_200g_2015-03-12 13-53.txt
2015-03-12 13-53

Temp (labview C)	Loadcell Voltage	Voltage Solenoid	Voltage Pressure	time
25.036488	0.007092	1.029118	-0.995534	0.000000
24.017850	-0.000472	1.120206	-0.996850	0.003000
25.799874	0.009722	1.180712	-0.998494	0.004000
24.527282	0.009722	1.147828	-0.997836	0.005000
25.291006	0.011038	1.165586	-0.997178	0.006000
23.890456	0.028795	1.114287	-0.996521	0.007000
25.545468	-0.008364	1.071538	-0.997836	0.008000
23.890456	0.006434	1.047204	-0.998165	0.009000
23.890456	0.024849	1.032078	-0.998165	0.010000
24.654605	0.010380	1.061673	-0.996192	0.011000
25.291006	-0.005733	1.109355	-0.997178	0.012000
25.291006	0.027480	1.213267	-0.996850	0.013000
25.163754	0.018930	1.317837	-0.996192	0.014000
24.909208	-0.006720	1.453647	-0.997178	0.015000
24.654605	0.019916	1.582880	-0.996850	0.016000
24.781914	0.025507	1.677914	-0.995534	0.017000
24.654605	-0.003102	1.756506	-0.995205	0.018000
25.036488	0.020245	1.797611	-0.998823	0.019000
25.291006	0.022876	1.794980	-0.995863	0.020000
24.654605	-0.005733	1.750258	-0.995534	0.021000
25.545468	0.012682	1.671009	-0.994877	0.022000
24.781914	0.013997	1.577948	-0.996192	0.023000
25.163754	-0.003102	1.459566	-0.996850	0.024000
24.654605	0.027480	1.385578	-0.997836	0.025000
24.017850	0.029781	1.322112	-0.997178	0.026000
24.909208	-0.005404	1.278706	-0.997178	0.027000
24.909208	0.030439	1.288900	-0.998823	0.028000
25.418244	0.020903	1.318824	-0.996521	0.029000
24.399945	-0.005075	1.413529	-0.996192	0.030000
24.781914	0.029453	1.505275	-0.998165	0.031000
24.527282	0.031754	1.630562	-0.999480	0.032000
23.890456	0.000186	1.728555	-0.997507	0.033000
24.145229	-0.004746	1.797611	-0.994877	0.034000
23.380738	0.031426	1.866009	-0.996521	0.035000
24.654605	-0.003431	1.872257	-0.997836	0.036000
24.527282	0.017614	1.857131	-0.996850	0.037000
24.272594	0.031426	1.784786	-0.994548	0.038000
24.527282	-0.001129	1.699289	-0.995534	0.039000
24.909208	0.005776	1.590115	-0.994219	0.040000
25.036488	0.011367	1.474693	-0.997836	0.041000
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

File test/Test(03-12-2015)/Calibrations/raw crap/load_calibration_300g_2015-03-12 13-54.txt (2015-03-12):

load_calibration_300g_2015-03-12 13-54.txt
2015-03-12 13-54

Temp (labview C)	Loadcell Voltage	Voltage Solenoid	Voltage Pressure	time
23.763048	0.009722	0.276738	-0.997178	0.000000
24.654605	-0.006062	0.498704	-0.996521	0.003000
24.654605	0.022547	0.681208	-0.996192	0.004000
24.781914	0.011038	0.840694	-0.997178	0.005000
25.163754	0.021561	1.037339	-0.998165	0.006000
25.545468	-0.000800	1.218200	-0.997178	0.007000
24.909208	-0.003102	1.352694	-0.997178	0.008000
24.527282	0.024191	1.474364	-0.996192	0.009000
24.527282	0.021561	1.535857	-0.994548	0.010000
24.527282	-0.003431	1.561177	-0.997507	0.011000
25.545468	0.027151	1.531582	-0.997507	0.012000
24.272594	0.028795	1.480612	-0.995534	0.013000
24.272594	0.029781	1.410241	-0.997507	0.014000
24.909208	0.016299	1.306986	-0.997178	0.015000
25.418244	0.033070	1.250426	-0.996850	0.016000
24.272594	0.013997	1.201758	-0.997178	0.017000
24.145229	0.029124	1.184329	-0.994877	0.018000
25.545468	0.015970	1.211623	-0.997178	0.019000
23.763048	0.004132	1.272129	-0.996521	0.020000
24.781914	0.034056	1.373411	-0.996192	0.021000
23.890456	0.031097	1.471076	-0.995863	0.022000
24.781914	0.006763	1.608201	-0.996850	0.023000
25.672678	-0.003102	1.696987	-0.995534	0.024000
24.527282	0.008078	1.771633	-0.996521	0.025000
24.527282	0.034714	1.838058	-0.996192	0.026000
24.145229	0.012682	1.840360	-0.995863	0.027000
25.291006	-0.003102	1.824247	-0.995863	0.028000
23.890456	0.033399	1.741709	-0.997507	0.029000
25.418244	0.019916	1.662130	-0.995534	0.030000
24.272594	0.016957	1.543420	-0.995863	0.031000
24.272594	0.032741	1.446413	-0.996521	0.032000
24.399945	0.010709	1.372096	-0.996521	0.033000
24.909208	0.006434	1.313891	-0.996521	0.034000
24.654605	0.015641	1.293832	-0.997507	0.035000
25.545468	0.013997	1.313891	-0.994877	0.036000
24.399945	0.004461	1.377686	-0.995534	0.037000
24.781914	0.031097	1.471076	-0.994219	0.038000
25.545468	0.014326	1.573344	-0.996521	0.039000
24.654605	0.018930	1.695343	-0.996521	0.040000
24.399945	0.037345	1.777552	-0.996192	0.041000
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

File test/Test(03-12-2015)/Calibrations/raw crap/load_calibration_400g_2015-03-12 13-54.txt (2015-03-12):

load_calibration_400g_2015-03-12 13-54.txt
2015-03-12 13-54

Temp (labview C)	Loadcell Voltage	Voltage Solenoid	Voltage Pressure	time
25.418244	0.000186	0.852861	-0.998823	0.000000
24.145229	0.001830	0.894295	-0.997178	0.003000
23.508189	-0.001458	0.919615	-0.996521	0.004000
25.036488	0.013340	0.899885	-0.995205	0.005000
24.909208	-0.000143	0.897254	-0.995863	0.006000
25.163754	0.030439	0.904489	-0.995863	0.007000
24.781914	0.023534	0.955130	-0.996850	0.008000
24.909208	0.002159	1.019253	-0.996521	0.009000
24.527282	0.036029	1.140923	-0.994219	0.010000
24.399945	0.018601	1.262593	-0.995534	0.011000
23.890456	0.008078	1.406623	-0.996192	0.012000
24.145229	0.034714	1.539474	-0.997178	0.013000
24.909208	0.038331	1.635823	-0.996192	0.014000
24.781914	0.011367	1.722307	-0.997178	0.015000
23.890456	0.018601	1.765714	-0.996192	0.016000
24.909208	0.020903	1.766043	-0.997507	0.017000
24.527282	0.002159	1.721321	-0.994877	0.018000
24.527282	0.026822	1.645688	-0.997836	0.019000
24.781914	0.035701	1.561177	-0.996850	0.020000
24.909208	0.021889	1.449043	-0.995205	0.021000
24.909208	0.018272	1.342500	-0.998494	0.022000
24.527282	0.038660	1.310274	-0.998823	0.023000
23.890456	0.038989	1.275089	-0.996850	0.024000
24.399945	0.019587	1.285940	-0.997178	0.025000
22.488179	0.030439	1.316851	-0.997178	0.026000
24.145229	0.003803	1.413529	-0.997178	0.027000
24.272594	0.024849	1.503302	-0.995863	0.028000
24.145229	0.026822	1.623327	-0.994219	0.029000
25.163754	0.042277	1.724938	-0.993890	0.030000
24.145229	0.013011	1.801228	-0.994877	0.031000
25.418244	0.003803	1.862063	-0.995534	0.032000
24.527282	0.039647	1.875874	-0.998494	0.033000
25.291006	0.010051	1.859761	-0.994219	0.034000
24.909208	0.004132	1.788732	-0.996192	0.035000
25.291006	0.029124	1.704550	-0.997507	0.036000
25.672678	0.033070	1.599322	-0.996521	0.037000
24.399945	0.001501	1.484229	-0.997507	0.038000
24.781914	0.037345	1.404979	-0.996192	0.039000
24.909208	0.015641	1.337568	-0.997836	0.040000
25.291006	0.002159	1.307315	-0.996850	0.041000
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

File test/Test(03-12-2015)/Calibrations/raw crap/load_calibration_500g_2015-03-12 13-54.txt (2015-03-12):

load_calibration_500g_2015-03-12 13-54.txt
2015-03-12 13-54

Temp (labview C)	Loadcell Voltage	Voltage Solenoid	Voltage Pressure	time
25.291006	0.043593	0.780517	-0.995534	0.000000
24.909208	0.013668	0.943292	-0.994548	0.003000
24.145229	0.045566	1.079430	-0.996521	0.004000
25.163754	0.012682	1.176437	-0.997507	0.005000
26.308517	0.032083	1.241218	-0.995205	0.006000
24.781914	0.042606	1.228065	-0.995205	0.007000
24.017850	0.008407	1.205375	-0.997178	0.008000
25.927056	0.025835	1.141581	-0.997836	0.009000
25.799874	0.028466	1.095872	-0.995863	0.010000
24.145229	0.014655	1.061673	-0.995205	0.011000
25.163754	0.042277	1.044574	-0.996850	0.012000
24.909208	0.034385	1.074827	-0.997836	0.013000
24.527282	0.033399	1.122837	-0.998165	0.014000
24.909208	0.042277	1.226749	-0.994877	0.015000
25.291006	0.016957	1.333622	-0.996850	0.016000
23.890456	0.045237	1.469431	-0.996850	0.017000
24.272594	0.046881	1.595376	-0.995863	0.018000
24.399945	0.014326	1.689752	-0.997836	0.019000
24.909208	0.043921	1.769331	-0.996521	0.020000
23.890456	0.019259	1.807805	-0.994877	0.021000
24.909208	0.026822	1.803201	-0.995534	0.022000
23.763048	0.047539	1.759795	-0.995863	0.023000
23.380738	0.016957	1.677914	-0.993561	0.024000
24.654605	0.023534	1.585511	-0.994877	0.025000
24.781914	0.042935	1.472062	-0.994877	0.026000
25.036488	0.013340	1.391826	-0.997836	0.027000
24.399945	0.010380	1.324743	-0.995863	0.028000
24.145229	0.045894	1.283967	-0.997507	0.029000
25.291006	0.016628	1.296463	-0.995534	0.030000
24.909208	0.028466	1.325072	-0.996521	0.031000
23.635625	0.048196	1.423065	-0.996850	0.032000
25.672678	0.013997	1.511523	-0.995534	0.033000
24.654605	0.026493	1.636481	-0.996850	0.034000
25.418244	0.016628	1.738749	-0.997178	0.035000
24.909208	0.011367	1.811751	-0.994548	0.036000
23.890456	0.046552	1.875546	-0.995863	0.037000
23.635625	0.022218	1.883109	-0.996192	0.038000
24.272594	0.009065	1.864365	-0.994877	0.039000
24.654605	0.045566	1.789719	-0.997836	0.040000
24.017850	0.022876	1.704879	-0.995534	0.041000
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

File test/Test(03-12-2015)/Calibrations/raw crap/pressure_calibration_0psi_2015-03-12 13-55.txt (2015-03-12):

pressure_calibration_0psi_2015-03-12 13-55.txt
2015-03-12 13-55

Temp (labview C)	Loadcell Voltage	Voltage Solenoid	Voltage Pressure	time
24.145229	0.025507	0.141915	-0.997507	0.000000
25.036488	0.002817	0.322118	-0.998165	0.003000
24.399945	0.027480	0.523366	-0.996850	0.004000
24.527282	0.001173	0.722642	-0.996521	0.005000
25.291006	0.022547	0.935400	-0.996521	0.006000
24.909208	0.024520	1.125796	-0.998494	0.007000
24.527282	0.002159	1.277719	-0.995863	0.008000
24.017850	0.020903	1.412543	-0.996521	0.009000
24.017850	0.029124	1.493436	-0.999480	0.010000
24.527282	0.007421	1.525991	-0.997836	0.011000
24.145229	-0.010008	1.517113	-0.993561	0.012000
26.054223	-0.004746	1.466143	-0.995205	0.013000
24.909208	0.026493	1.406295	-0.996192	0.014000
24.654605	-0.007048	1.305013	-0.996850	0.015000
23.253273	0.027480	1.243849	-0.997507	0.016000
23.380738	0.026493	1.197154	-0.995863	0.017000
25.163754	0.000186	1.166243	-0.996521	0.018000
25.672678	0.029453	1.189591	-0.997507	0.019000
24.017850	0.003146	1.228065	-0.996521	0.020000
25.545468	0.010051	1.334279	-0.998494	0.021000
24.909208	0.019916	1.429971	-0.995863	0.022000
24.909208	0.022876	1.563479	-0.995205	0.023000
24.781914	-0.005075	1.669036	-0.995205	0.024000
24.399945	0.032083	1.754862	-0.994548	0.025000
25.672678	0.002488	1.821945	-0.995534	0.026000
24.781914	0.006763	1.834441	-0.995534	0.027000
24.781914	0.022218	1.822274	-0.993561	0.028000
24.527282	0.019587	1.758151	-0.995534	0.029000
24.527282	0.006434	1.671337	-0.996521	0.030000
24.909208	0.021561	1.571042	-0.995863	0.031000
25.163754	-0.000143	1.454963	-0.997507	0.032000
24.145229	-0.008364	1.382289	-0.996192	0.033000
24.781914	-0.003760	1.319810	-0.997178	0.034000
25.799874	0.013340	1.288242	-0.994877	0.035000
24.654605	-0.008364	1.304684	-0.995205	0.036000
24.272594	0.021561	1.354338	-0.995534	0.037000
25.291006	0.016299	1.446413	-0.996192	0.038000
24.781914	-0.004418	1.608858	-0.996850	0.039000
24.145229	0.025835	1.678243	-0.994877	0.040000
26.308517	0.001173	1.744668	-0.997178	0.041000
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

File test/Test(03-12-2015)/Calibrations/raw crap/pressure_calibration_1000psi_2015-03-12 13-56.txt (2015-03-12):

pressure_calibration_1000psi_2015-03-12 13-56.txt
2015-03-12 13-56

Temp (labview C)	Loadcell Voltage	Voltage Solenoid	Voltage Pressure	time
25.672678	-0.032369	0.459901	-1.810395	0.000000
26.181377	-0.009679	0.559538	-1.813026	0.003000
25.545468	0.005119	0.642406	-1.811382	0.004000
24.654605	0.005119	0.703240	-1.810066	0.005001
24.527282	-0.030396	0.726917	-1.812368	0.006001
25.291006	-0.027436	0.676933	-1.812039	0.007000
26.308517	-0.032369	0.629581	-1.812368	0.008001
24.272594	-0.002773	0.542439	-1.812697	0.009001
25.036488	0.000515	0.468779	-1.812697	0.010001
26.562754	-0.026450	0.415837	-1.811053	0.011001
24.145229	-0.031711	0.371115	-1.811382	0.012001
23.890456	-0.021846	0.368813	-1.813026	0.013001
25.291006	-0.007377	0.403670	-1.812697	0.014001
24.145229	-0.028094	0.503307	-1.812368	0.015001
24.654605	-0.028752	0.567431	-1.811710	0.016002
24.781914	0.006763	0.687456	-1.812697	0.017002
23.635625	-0.015598	0.812086	-1.811053	0.018002
26.308517	-0.024806	0.901529	-1.810066	0.019002
25.163754	0.002817	0.981437	-1.812697	0.020002
25.163754	-0.022175	1.023857	-1.812368	0.021002
24.781914	-0.031053	1.015965	-1.810724	0.022002
25.036488	-0.008035	0.985712	-1.813355	0.023002
23.508189	-0.030396	0.899885	-1.814012	0.024003
24.781914	-0.033027	0.803536	-1.812368	0.025002
24.781914	-0.001458	0.680879	-1.812697	0.026002
24.527282	-0.003431	0.604260	-1.810395	0.027003
23.508189	-0.010994	0.530930	-1.812368	0.028003
25.291006	-0.034013	0.480289	-1.813026	0.029003
24.781914	0.004790	0.483248	-1.813355	0.030003
24.527282	0.004790	0.506925	-1.813355	0.031003
25.163754	-0.029738	0.593080	-1.810395	0.032003
24.781914	-0.032040	0.676933	-1.812039	0.033003
24.654605	0.005776	0.799919	-1.813355	0.034003
25.291006	-0.029409	0.904160	-1.812697	0.035004
25.163754	-0.032698	0.976833	-1.811710	0.036004
24.017850	-0.006062	1.041614	-1.811382	0.037004
24.145229	0.005447	1.062002	-1.811382	0.038004
23.763048	-0.023161	1.045231	-1.813026	0.039004
24.399945	-0.032040	0.984396	-1.810724	0.040004
25.036488	-0.010666	0.898241	-1.811710	0.041004
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

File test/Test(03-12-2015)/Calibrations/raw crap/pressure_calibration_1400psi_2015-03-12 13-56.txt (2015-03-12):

pressure_calibration_1400psi_2015-03-12 13-56.txt
2015-03-12 13-56

Temp (labview C)	Loadcell Voltage	Voltage Solenoid	Voltage Pressure	time
25.291006	-0.013296	0.458257	-2.036307	0.000000
24.781914	-0.027436	0.519749	-2.036307	0.003000
24.654605	0.001830	0.561840	-2.036307	0.004000
24.017850	-0.012967	0.583215	-2.036307	0.005000
26.181377	-0.000143	0.576638	-2.036307	0.006001
25.163754	-0.038946	0.497717	-2.036307	0.007000
24.399945	-0.035328	0.427675	-2.036307	0.008000
25.545468	-0.003102	0.317185	-2.036307	0.009001
24.781914	-0.023161	0.237936	-2.036307	0.010001
23.125793	-0.035986	0.174470	-2.036307	0.011001
24.909208	-0.009021	0.128762	-2.036307	0.012001
24.781914	-0.001787	0.135338	-2.036307	0.013001
25.418244	-0.000800	0.161974	-2.036307	0.014001
25.418244	0.001501	0.239251	-2.036307	0.015001
24.781914	-0.034013	0.333956	-2.036307	0.016001
24.399945	-0.012967	0.456612	-2.036307	0.017002
25.672678	-0.034671	0.566773	-2.036307	0.018002
24.399945	0.002159	0.650626	-2.036307	0.019001
24.909208	-0.032698	0.719353	-2.036307	0.020002
23.890456	-0.035986	0.739413	-2.036307	0.021002
25.418244	-0.010994	0.726588	-2.036307	0.022002
24.527282	-0.001129	0.673316	-2.036307	0.023002
24.781914	-0.034013	0.585517	-2.036307	0.024002
23.890456	-0.016913	0.486865	-2.036307	0.025002
25.291006	0.000515	0.368484	-2.036307	0.026002
25.418244	-0.015598	0.292194	-2.036307	0.027002
24.399945	-0.035000	0.217876	-2.036307	0.028003
24.399945	-0.030067	0.181047	-2.036307	0.029003
25.036488	-0.035000	0.184006	-2.036307	0.030003
25.418244	-0.004418	0.208669	-2.036307	0.031003
23.763048	-0.014283	0.300415	-2.036307	0.032003
24.654605	-0.035328	0.385255	-2.036307	0.033003
24.145229	0.002817	0.513830	-2.036307	0.034003
23.508189	-0.018886	0.605576	-2.036307	0.035003
25.545468	-0.032040	0.677920	-2.036307	0.036004
24.909208	0.002817	0.747962	-2.036307	0.037004
26.435643	-0.013296	0.754868	-2.036307	0.038003
25.672678	-0.007377	0.737768	-2.036307	0.039004
24.527282	-0.012639	0.663451	-2.036307	0.040004
25.036488	-0.034342	0.574994	-2.036307	0.041004
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

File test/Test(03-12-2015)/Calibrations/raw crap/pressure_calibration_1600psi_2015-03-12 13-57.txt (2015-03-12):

pressure_calibration_1600psi_2015-03-12 13-57.txt
2015-03-12 13-57

Temp (labview C)	Loadcell Voltage	Voltage Solenoid	Voltage Pressure	time
24.909208	-0.011981	0.471081	-2.036307	0.000000
24.654605	0.001173	0.407287	-2.036307	0.003000
24.145229	-0.037301	0.296469	-2.036307	0.004001
23.763048	-0.016585	0.201106	-2.036307	0.005001
24.527282	-0.037301	0.124815	-2.036307	0.006001
24.654605	-0.010008	0.073846	-2.036307	0.007001
23.890456	-0.007706	0.074175	-2.036307	0.008001
24.654605	-0.024806	0.094234	-2.036307	0.009001
24.781914	-0.015927	0.177101	-2.036307	0.010001
24.527282	-0.027765	0.268189	-2.036307	0.011001
24.909208	-0.033027	0.378349	-2.036307	0.012002
25.036488	-0.032369	0.477000	-2.036307	0.013001
24.272594	0.004132	0.557237	-2.036307	0.014001
22.743268	-0.009021	0.616099	-2.036307	0.015002
24.399945	-0.034013	0.634513	-2.036307	0.016002
25.036488	-0.002116	0.618729	-2.036307	0.017002
25.672678	0.000844	0.560196	-2.036307	0.018002
25.799874	-0.036973	0.467135	-2.036307	0.019002
23.635625	-0.017900	0.366182	-2.036307	0.020002
25.036488	0.001501	0.245499	-2.036307	0.021002
24.781914	-0.024806	0.165591	-2.036307	0.022002
24.399945	-0.022504	0.092589	-2.036307	0.023003
25.163754	-0.000143	0.052471	-2.036307	0.024003
24.017850	-0.026779	0.062994	-2.036307	0.025002
25.418244	-0.023161	0.094234	-2.036307	0.026003
25.291006	0.002817	0.188939	-2.036307	0.027003
24.145229	-0.026121	0.276081	-2.036307	0.028003
25.291006	0.003146	0.411562	-2.036307	0.029003
25.672678	-0.000472	0.495744	-2.036307	0.030003
25.291006	-0.029409	0.569075	-2.036307	0.031003
24.017850	-0.029409	0.634842	-2.036307	0.032003
25.418244	-0.025463	0.616099	-2.036307	0.033003
24.017850	0.002817	0.596697	-2.036307	0.034004
25.927056	-0.033355	0.510213	-2.036307	0.035004
23.635625	0.000515	0.424386	-2.036307	0.036004
24.272594	-0.022175	0.308636	-2.036307	0.037004
25.418244	-0.034671	0.201435	-2.036307	0.038004
24.272594	-0.010666	0.128104	-2.036307	0.039004
24.909208	0.001173	0.066940	-2.036307	0.040004
24.654605	-0.036973	0.044250	-2.036307	0.041004
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

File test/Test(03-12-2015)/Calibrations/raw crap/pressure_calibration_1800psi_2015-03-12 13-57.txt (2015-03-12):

pressure_calibration_1800psi_2015-03-12 13-57.txt
2015-03-12 13-57

Temp (labview C)	Loadcell Voltage	Voltage Solenoid	Voltage Pressure	time
25.291006	-0.012967	0.226097	-2.426310	0.000000
25.418244	-0.005733	0.164934	-2.427625	0.003000
25.927056	-0.034342	0.073188	-2.428940	0.004000
23.890456	-0.005404	0.005776	-2.427625	0.005000
24.781914	-0.012310	-0.000472	-2.425652	0.006001
25.672678	-0.039603	0.009394	-2.425981	0.007000
24.527282	-0.035328	0.119883	-2.428940	0.008001
24.654605	-0.039932	0.169866	-2.427954	0.009001
25.036488	-0.040919	0.276738	-2.427954	0.010001
24.399945	-0.018558	0.366840	-2.428940	0.011001
24.654605	-0.002773	0.436553	-2.427625	0.012001
24.145229	-0.006720	0.489496	-2.429598	0.013001
24.654605	-0.041576	0.501992	-2.427296	0.014001
25.418244	-0.015927	0.480618	-2.427625	0.015001
24.654605	-0.003431	0.413206	-2.426967	0.016001
26.181377	-0.038617	0.317185	-2.429598	0.017002
24.527282	-0.011323	0.207025	-2.428940	0.018002
25.418244	-0.011652	0.092918	-2.426967	0.019002
24.145229	-0.021188	0.010709	-2.427296	0.020002
25.291006	-0.040261	-0.061307	-2.424337	0.021002
25.163754	-0.013296	-0.098794	-2.428940	0.022002
23.635625	-0.003431	-0.086298	-2.428940	0.023002
24.272594	-0.034671	-0.048153	-2.427296	0.024002
24.781914	-0.031053	0.041291	-2.426967	0.025002
24.145229	-0.009679	0.129419	-2.428612	0.026002
24.654605	-0.030396	0.257666	-2.426639	0.027002
24.527282	-0.040919	0.337902	-2.427954	0.028003
24.909208	-0.011652	0.412548	-2.427625	0.029003
24.399945	-0.001787	0.462203	-2.425981	0.030003
25.418244	-0.040919	0.458914	-2.425652	0.031003
25.418244	-0.027765	0.436224	-2.426967	0.032003
25.163754	-0.007377	0.347438	-2.428283	0.033003
24.017850	-0.018886	0.261612	-2.425981	0.034003
25.418244	-0.043220	0.140929	-2.428283	0.035003
24.527282	-0.006062	0.037674	-2.425323	0.036004
25.799874	-0.021188	-0.035986	-2.428612	0.037004
25.545468	-0.037630	-0.099452	-2.427296	0.038003
24.399945	-0.029080	-0.114249	-2.427296	0.039004
25.163754	-0.003102	-0.096163	-2.426310	0.040004
25.418244	-0.019544	-0.034671	-2.427954	0.041004
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

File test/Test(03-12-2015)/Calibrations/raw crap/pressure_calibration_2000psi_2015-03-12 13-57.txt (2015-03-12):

pressure_calibration_2000psi_2015-03-12 13-57.txt
2015-03-12 13-57

Temp (labview C)	Loadcell Voltage	Voltage Solenoid	Voltage Pressure	time
25.672678	-0.021846	0.506596	-2.541403	0.000000
24.781914	-0.044865	0.392489	-2.541403	0.005001
24.272594	-0.009679	0.279698	-2.541403	0.006001
24.527282	-0.019544	0.139613	-2.541403	0.007001
24.527282	-0.042892	0.038660	-2.541403	0.008001
25.036488	-0.006720	-0.051441	-2.541403	0.009001
24.781914	-0.031382	-0.101754	-2.541403	0.010001
25.418244	-0.037959	-0.105042	-2.541403	0.011001
25.036488	-0.005075	-0.078735	-2.541403	0.012001
26.562754	-0.034671	0.004790	-2.541403	0.013001
26.308517	-0.033355	0.076476	-2.541403	0.014001
27.325133	-0.042892	0.190912	-2.541403	0.015002
25.291006	-0.036315	0.264900	-2.541403	0.016002
25.545468	-0.015927	0.335600	-2.541403	0.017002
24.272594	-0.003431	0.388872	-2.541403	0.018002
26.181377	-0.029080	0.386570	-2.541403	0.019002
26.181377	-0.005075	0.364867	-2.541403	0.020002
24.909208	-0.028423	0.279369	-2.541403	0.021002
23.890456	-0.043878	0.187623	-2.541403	0.022002
24.654605	-0.010994	0.070228	-2.541403	0.023002
26.308517	-0.006720	-0.037959	-2.541403	0.024003
24.399945	-0.042234	-0.120168	-2.541403	0.025002
24.527282	-0.019873	-0.187251	-2.541403	0.026003
24.017850	-0.005404	-0.210599	-2.541403	0.027003
26.181377	-0.039274	-0.197445	-2.541403	0.028003
24.781914	-0.043220	-0.144502	-2.541403	0.029003
24.272594	-0.009679	-0.057032	-2.541403	0.030003
25.036488	-0.031053	0.045566	-2.541403	0.031003
25.291006	-0.041576	0.159672	-2.541403	0.032003
24.654605	-0.010994	0.239909	-2.541403	0.033003
24.145229	-0.024806	0.313239	-2.541403	0.034003
25.927056	-0.038617	0.348096	-2.541403	0.035004
24.527282	-0.030396	0.335600	-2.541403	0.036004
24.654605	-0.042234	0.308307	-2.541403	0.037004
24.781914	-0.010994	0.215903	-2.541403	0.038004
24.654605	-0.016913	0.128433	-2.541403	0.039004
25.799874	-0.007048	-0.004089	-2.541403	0.040004
26.181377	-0.019215	-0.093204	-2.541403	0.041004
24.527282	-0.041905	-0.171796	-2.541403	0.042004
26.181377	-0.009679	-0.228027	-2.541403	0.043005
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

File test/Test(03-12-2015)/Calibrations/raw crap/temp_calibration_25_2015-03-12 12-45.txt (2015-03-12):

temp_calibration2015-03-12 12-45.txt
2015-03-12 12-45

Temp (labview C)	time
27.579149	0.000000
27.706136	0.067000
26.181377	0.077000
28.594659	0.087000
25.418244	0.097000
26.181377	0.107000
26.944006	0.117000
25.799874	0.127000
25.799874	0.137000
27.071063	0.147000
26.562754	0.157000
27.071063	0.167000
25.163754	0.177000
25.545468	0.187000
26.816936	0.197000
26.054223	0.207000
26.562754	0.217000
25.036488	0.227000
27.579149	0.237000
27.198105	0.247000
26.054223	0.257000
26.944006	0.267000
26.435643	0.277000
28.087014	0.287000
26.562754	0.297000
26.308517	0.307000
27.198105	0.317000
25.418244	0.327000
26.944006	0.337000
26.689852	0.347000
26.689852	0.357000
27.071063	0.367000
26.054223	0.377000
26.054223	0.387000
26.562754	0.397000
26.181377	0.407000
26.308517	0.417000
26.181377	0.427000
25.672678	0.437000
26.435643	0.447000
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

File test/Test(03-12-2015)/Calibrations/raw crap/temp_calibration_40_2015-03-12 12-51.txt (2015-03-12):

temp_calibration2015-03-12 12-51.txt
2015-03-12 12-51

Temp (labview C)	time
38.073521	0.000000
37.443864	1.000200
38.325295	1.999400
38.702863	2.999600
38.073521	3.999800
38.954512	5.000000
38.828694	6.000200
39.583418	7.000400

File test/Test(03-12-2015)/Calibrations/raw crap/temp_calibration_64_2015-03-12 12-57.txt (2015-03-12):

temp_calibration_642015-03-12 12-57.txt
2015-03-12 12-57

Temp (labview C)	time
59.182538	0.000000
57.694079	0.003000
57.445857	0.004000
57.818174	0.005001
57.818174	0.006001
57.942259	0.007000
58.562528	0.008001
57.321731	0.009001
58.314451	0.010001
55.831397	0.011001
57.694079	0.012001
57.818174	0.013001
57.818174	0.014001
56.949289	0.015001
57.073447	0.016002
57.321731	0.017002
57.445857	0.018002
56.949289	0.019002
59.306510	0.020002
57.942259	0.021002
57.321731	0.022002
57.818174	0.023002
58.066333	0.024002
58.190397	0.025002
57.942259	0.026002
56.700942	0.027002
57.445857	0.028003
57.569973	0.029003
58.190397	0.030003
57.569973	0.031003
57.445857	0.032003
56.328343	0.033003
57.569973	0.034003
58.562528	0.035003
57.818174	0.036004
58.066333	0.037004
57.818174	0.038003
57.445857	0.039004
58.314451	0.040004
58.810563	0.041004
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

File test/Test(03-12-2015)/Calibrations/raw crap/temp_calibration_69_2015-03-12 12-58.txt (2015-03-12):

temp_calibration_69_2015-03-12 12-58.txt
2015-03-12 12-58

Temp (labview C)	time
61.164861	0.000000
61.288670	0.003000
60.917212	0.004001
61.164861	0.005001
61.783807	0.006001
61.412469	0.007001
61.041042	0.008001
60.917212	0.009001
60.917212	0.010001
60.297914	0.011001
61.536259	0.012002
61.783807	0.013001
61.288670	0.014001
61.041042	0.015002
61.660038	0.016002
62.278785	0.017002
61.660038	0.018002
60.545664	0.019002
61.412469	0.020002
62.649914	0.021002
60.793373	0.022002
61.660038	0.023003
61.288670	0.024003
60.793373	0.025002
60.793373	0.026003
60.917212	0.027003
63.020954	0.028003
59.554422	0.029003
61.288670	0.030003
60.793373	0.031003
61.660038	0.032003
62.031316	0.033003
62.031316	0.034004
61.660038	0.035004
60.669523	0.036004
61.907567	0.037004
61.164861	0.038004
61.660038	0.039004
61.164861	0.040004
61.164861	0.041004
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

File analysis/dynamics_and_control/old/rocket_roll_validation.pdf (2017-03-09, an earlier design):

close all
clear

%import all trial data and split the runs and time start at zero

data = importdata('C:\Users\kenny\Desktop\Rotational Rocket Model Validation\data.txt'); state0 = data(:,1);
state0 = state0(8:end);
time0 = data(:,3);
time0 = time0(8:end);
time0 = time0 - time0(1);
vel0 = data(:,2)*-1;
vel0 = vel0(8:end);

data = importdata('C:\Users\kenny\Desktop\Rotational Rocket Model Validation\impulse1.txt'); state1 = data(:,1);
time1 = data(:,3);
vel1 = data(:,2);

state11 = state1(8:2924);
time11 = time1(8:2924);
time11 = time11 - time11(1); vel11 = vel1(8:2924)*-1;

state12 = state1(2925:end); time12 = time1(2925:end);
time12 = time12 - time12(1);
vel12 = vel1(2925:end);

data = importdata('C:\Users\kenny\Desktop\Rotational Rocket Model Validation\impulse2.txt'); state2 = data(:,1);
time2 = data(:,3);
time2 = time2 - time2(1);
vel2 = data(:,2);

data = importdata('C:\Users\kenny\Desktop\Rotational Rocket Model Validation\impulse3.txt'); state3 = data(:,1);
time3 = data(:,3);
vel3 = data(:,2);

state31 = state3(1:2945);
time31 = time3(1:2945);
time31 = time31 - time31(1); vel31 = vel3(1:2945);

state32 = state3(2946:end); time32 = time3(2946:end);
time32 = time32 - time32(1); vel32 = vel3(2946:end);

%Graph all the collected data figure plot(time0,vel0,time0,state0) legend('Velocity (rad/s)','Duty Cycle State') title('Impulse Data')

figure
plot(time11,vel11,time11,state11) legend('Velocity (rad/s)','Duty Cycle State') title('Impulse Data 11')

figure
plot(time12,vel12,time12,state12) legend('Velocity (rad/s)','Duty Cycle State') title('Step Data 12')

figure
plot(time2,vel2,time2,state2) legend('Velocity (rad/s)','Duty Cycle State') title('Step Data 2')

figure
plot(time31,vel31,time31,state31) legend('Velocity (rad/s)','Duty Cycle State') title('Step Data 3')

figure
plot(time32,vel32,time32,state32) legend('Velocity (rad/s)','Duty Cycle State') title('Step Data 3')

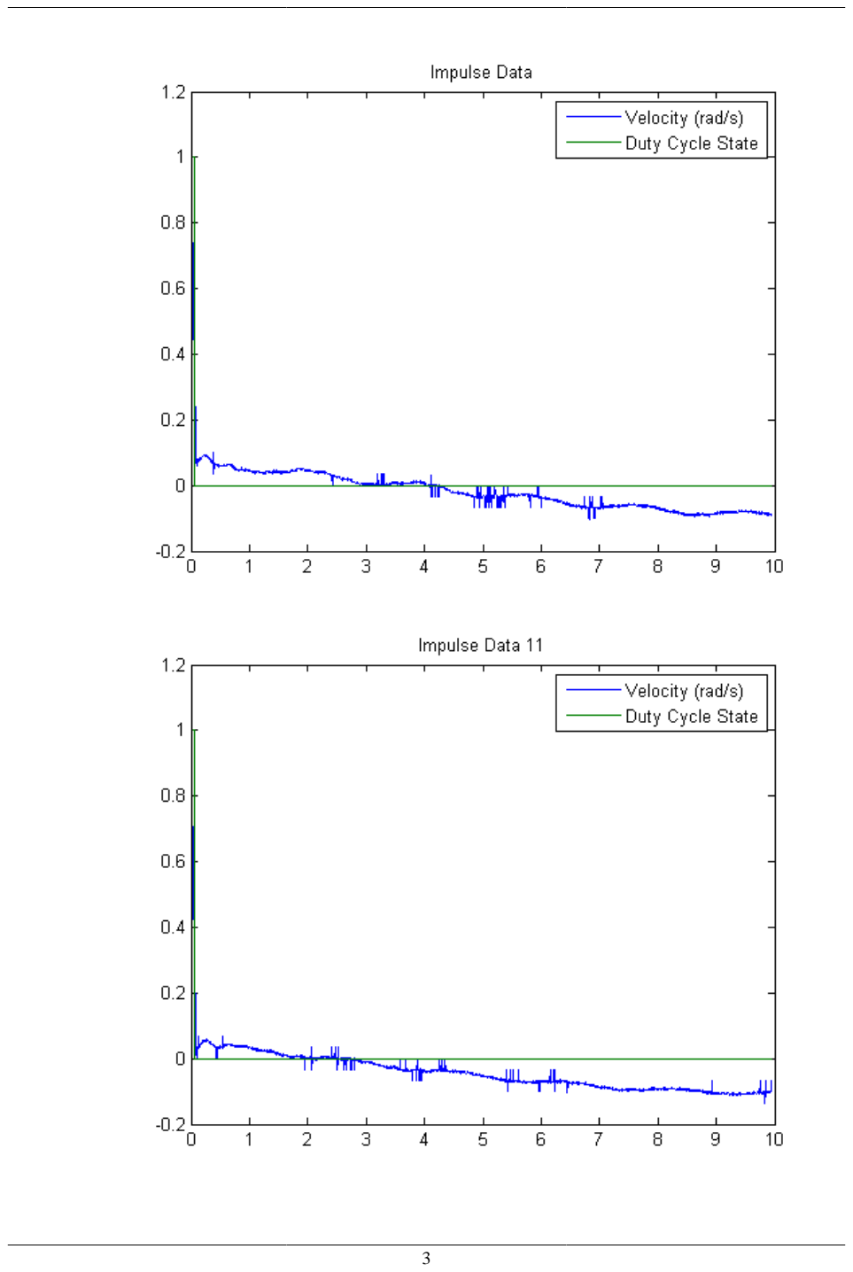
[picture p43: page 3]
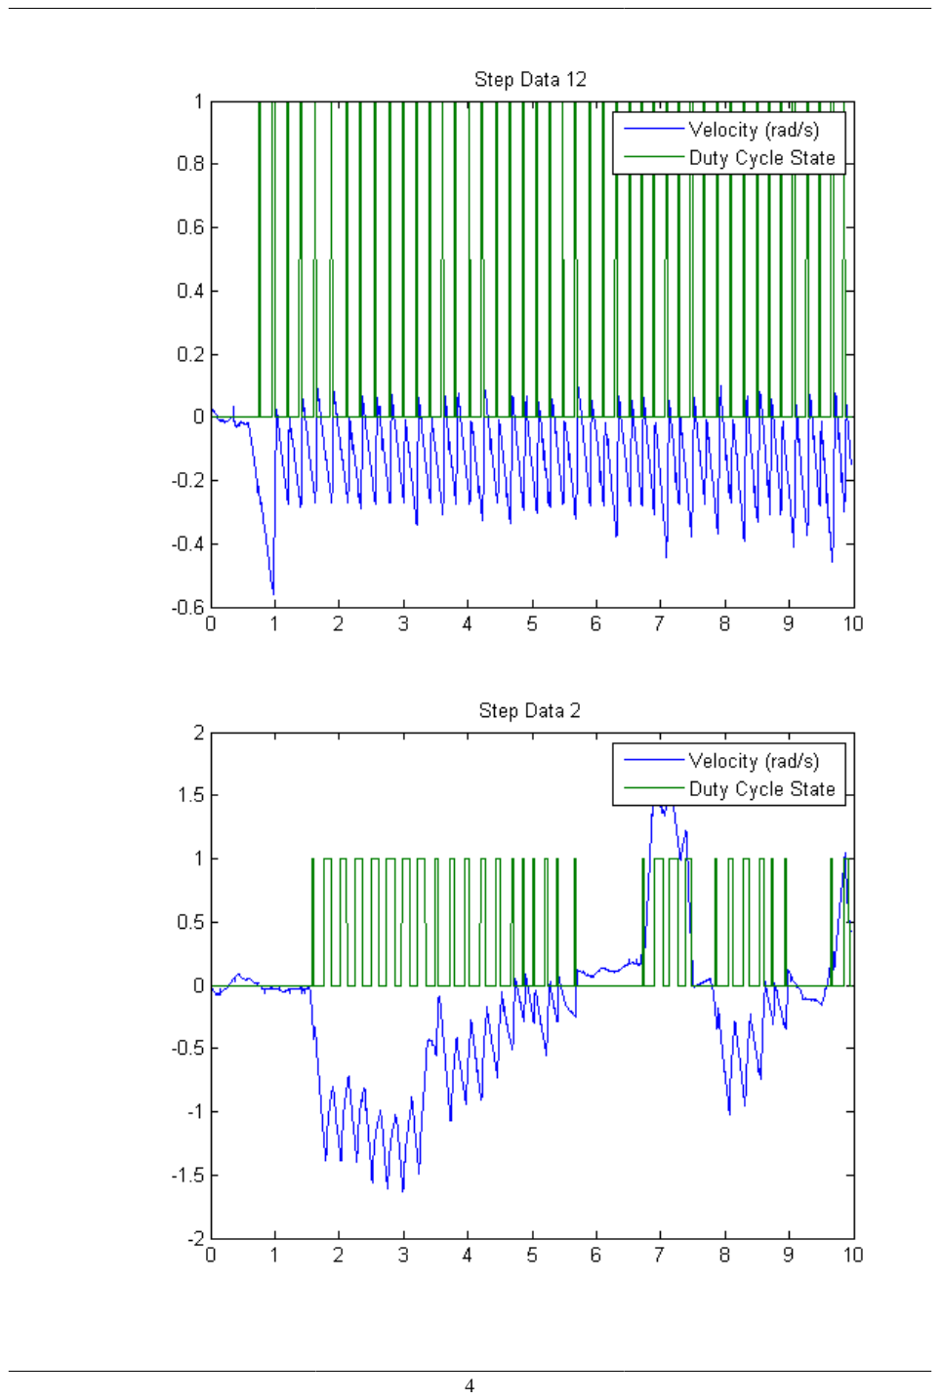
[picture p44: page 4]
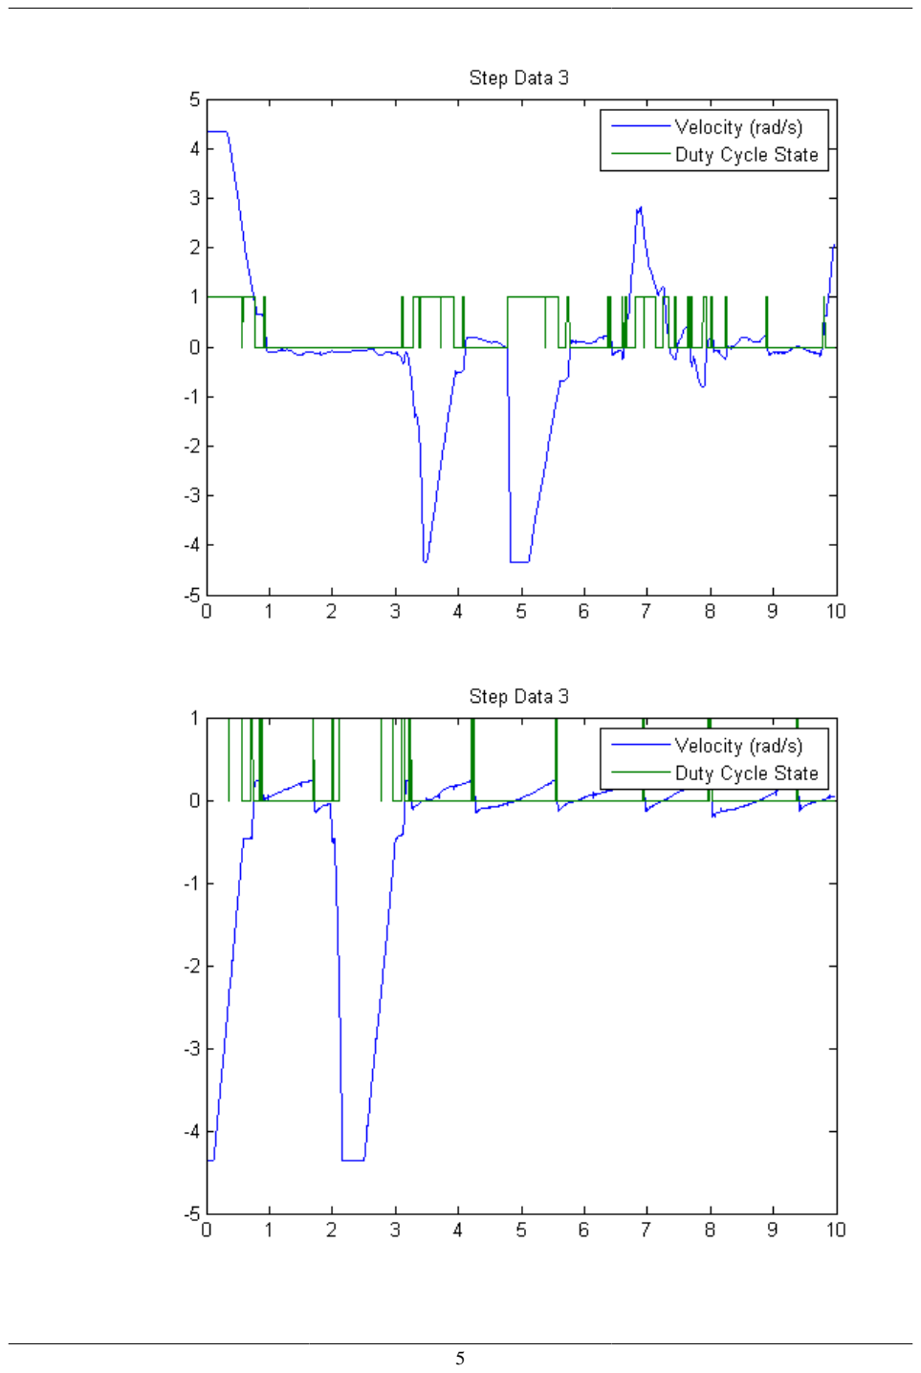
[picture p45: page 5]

%define variables
I = 0.0198;
Ftot = 11;
fr = 2.75*.0254;
b = 0.002;
a = 2; %I/(Ftot*ct*fr)
ct = 0.2;
Tau = 0.02;
hz = 10;
delay = 2.1;

simout = sim('rotational_system_sim.slx');

figure
plot(theta_dot.time,theta_dot.signals.values)
title('Step response of Theta Dot (rad/s)')

figure
plot(error.time,error.signals.values,time0,vel0,time11,vel11) legend('Simulation','Experimental 1','Experimental 2') title('Disturbance Rejection of Error (rad/s)')
xlim([0 .5])

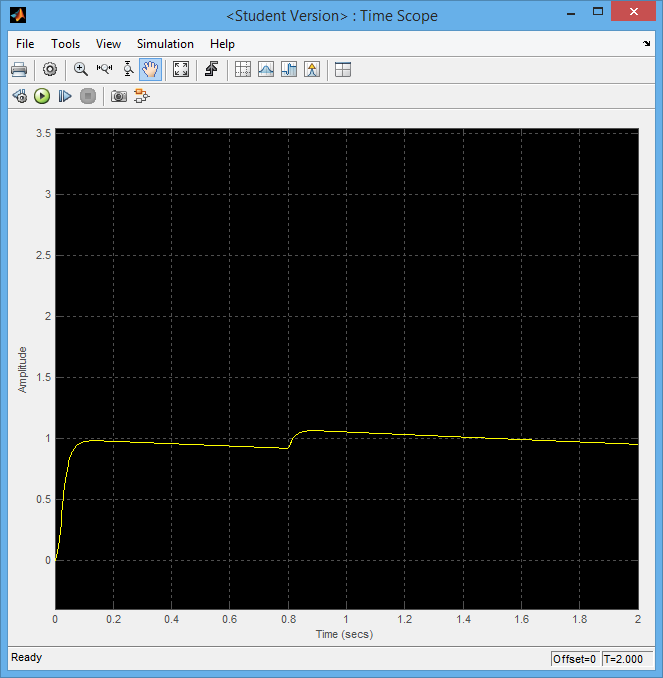
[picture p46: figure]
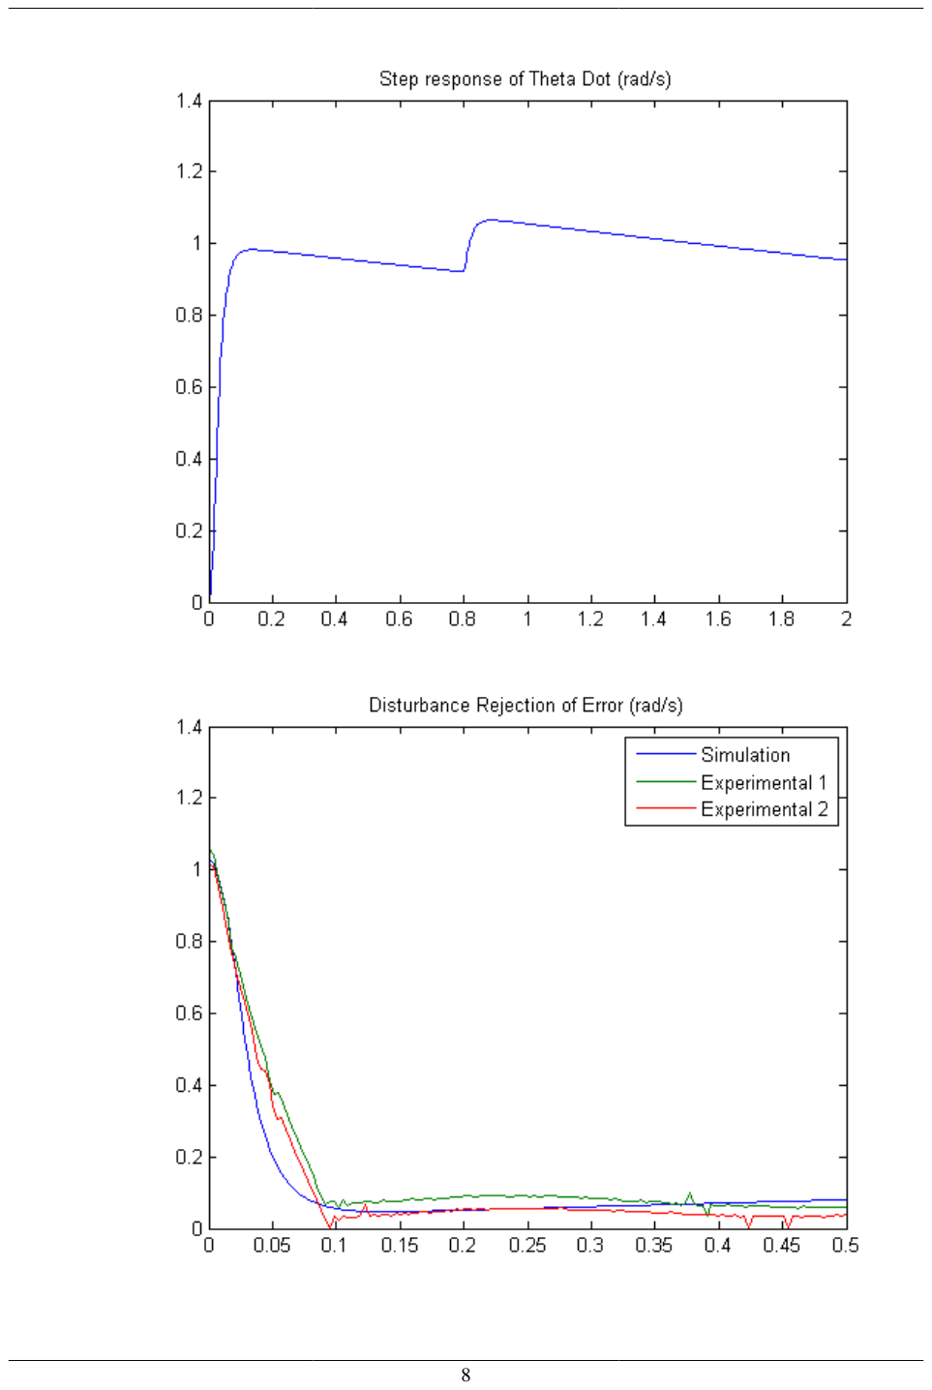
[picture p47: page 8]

Published with MATLAB® R2013a

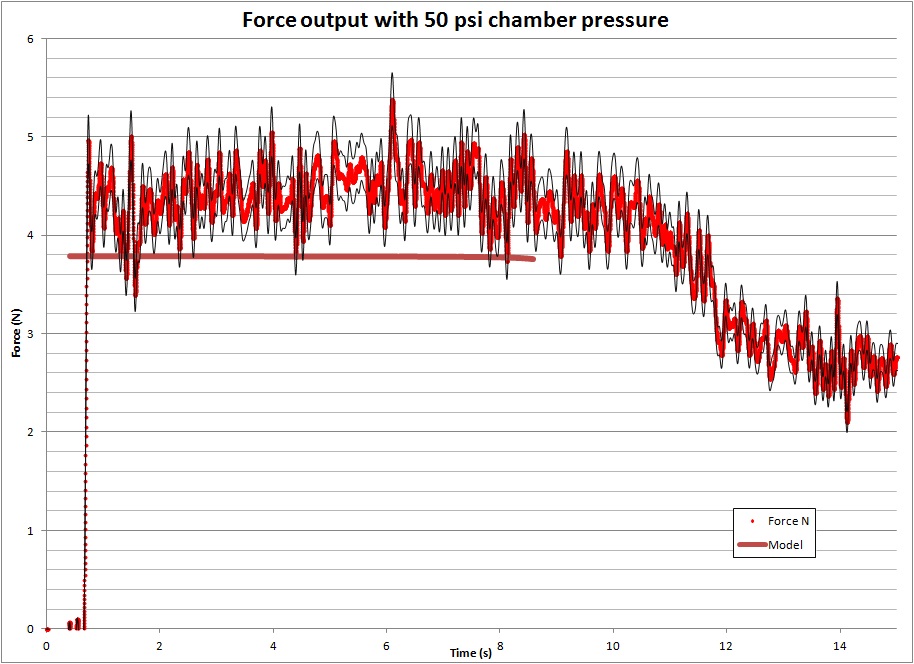
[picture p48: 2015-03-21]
test/Test(03-12-2015)/Pictures/Force with error 50psi.jpg

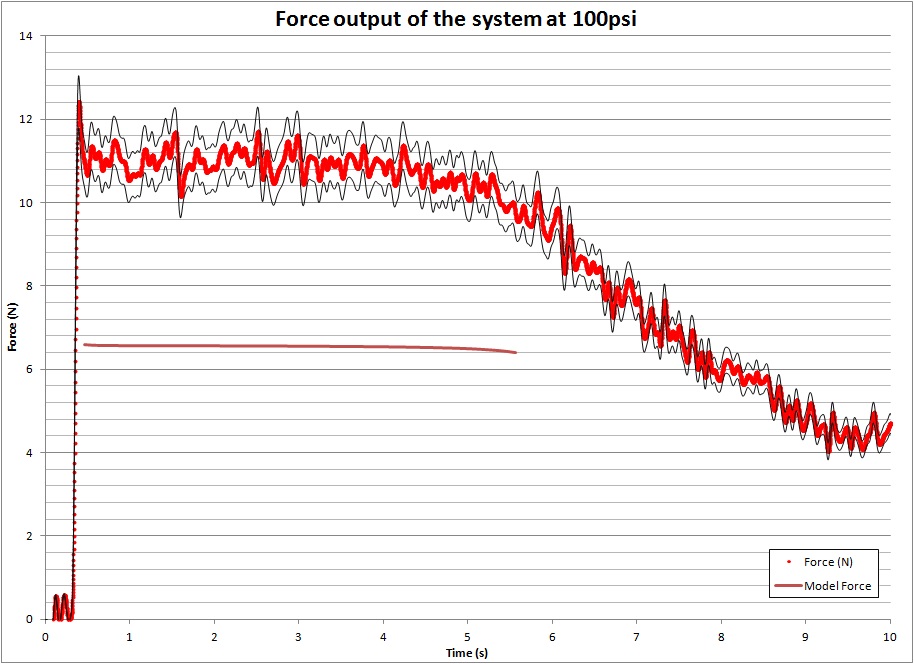
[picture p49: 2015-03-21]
test/Test(03-12-2015)/Pictures/Force with error 100psi.jpg

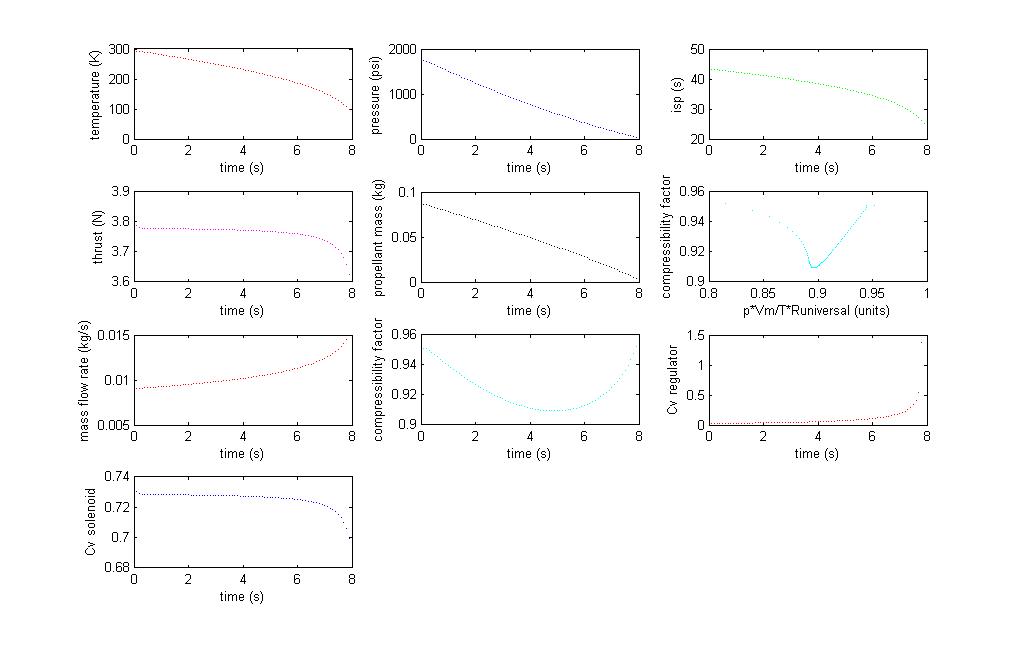
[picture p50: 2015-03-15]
test/Test(03-12-2015)/filtered data/1750 initial 50psi.jpg

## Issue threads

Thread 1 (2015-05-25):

Having trouble getting python module MRAA to play nice with Edison Arduino shield

jalouke, 2015-05-25:
the python module MRAA is for controlling i2c and gpio on the edison. I can get it to work fine with the mini breakout board.  However when I am using the Arduino shield, and I try to initialize a gpio pin it returns an error:

Traceback (most recent call last):
  File "blink.py", line 5, in <module>
    x = mraa.Gpio(54)
  File "/usr/local/lib/i386-linux-gnu/python2.7/site-packages/mraa.py", line 73_
    this = _mraa.new_Gpio(pin, owner, raw)
ValueError: Invalid GPIO pin specified

from the research I have been doing, it should be possible to use gpio commands on the arduino shield but I am probably missing a setting.

Also when I set raw = True the code doesnt return an error, but it also doesn't output either.

If this can't be fixed then it is not the end of the world, but we will need a new mosfet board with level shifting

jalouke, 2015-05-25:
I found this website that has a bunch of tables for selecting and setting values in the linux terminal, but I have no idea how to use it and if possible I would like help figuring it out.

http://www.emutexlabs.com/project/215-intel-edison-gpio-pin-multiplexing-guide

BartMassey, 2015-05-26:
I can read the tables, and follow the examples. What do you want help with?

It is possible that mraa.Gpio() is/isn't already doing the mapping between Edison GPIO pin numbers and Arduino shield pin numbers. Try both the raw and mapped pins here...

Closed 2016-05-19.

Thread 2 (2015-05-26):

Does the mosfet board we currently have require 3.3V  or can it run off 5V?

theschweizer, 2015-05-26:
Hey guys I'm working on an AVR microcontroller for the inverted pendulum simulation of pitch and yaw and my board is using 5V.  Can the mosfet board handle that?  I noticed in eagle that there is a pin for 5V and a pin for 3.3V but the schematic refers to the 3.3V only.

andrewgreenberg, 2015-05-26:
First, I assume you're talking about the  Solenoid Controller board.

Second, I'm not sure what you're really asking, so I'll tell you about it, and hopefully that'll answer your question.

The solenoid controller only needs 3.3V, it doesn't need 5V. It gets the 3.3V from the "3.3V" pin that should always be provided on any  "Arduino Uno-compatible board" the solenoid controller is attached to. So while you power the Arduino with 5V, it makes the 3.3V which then powers the solenoid controller.

That all said: the solenoid controller doesn't give a rats ass what voltage it uses. If you need to plug in 5, or even 7 volts into the 3.3V line, the solenoid controller won't care, that's totally fine. Don't use anything above 10 V, though, or you risk doing bad things to the MOSFET. Why this is a terrible idea: if you put 5 or 10V on that pin from an external supply, and then plug in the solenoid controller board into an actual Arduino, you'll totally fry the Arduino.

theschweizer, 2015-05-26:
Sorry for not being clearer.  I was referring to the solenoid control board.  I am not using an Arduino i am using an ATmega88PA MCU and it uses 5V.  I have a voltage regulator on my breadboard to convert a 9V battery power source down to 5V.  I needed to know if I need to also regulated the voltage to 3.3V for the sake of the Solenoid Controller board but it sound like I can put 5V in and be fine.

thanks.

andrewgreenberg, 2015-05-26:
Yep, that's fine. Although now I'm curious, why are you using an ATMega88? I thought we were transitioning to Edison and/or BBB?

theschweizer, 2015-05-26:
This is purely for show of the inverted pendulum test.  Using the
atmega88pa let's me satisfy a required project for my microcontroller class
and do work on our capstone project.  I believe Jeremy is working on
porting the roll controller to the edison from arduino.
On May 26, 2015 10:16 AM, "Andrew Greenberg" <notifications@github.com>
wrote:

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

andrewgreenberg, 2015-05-26:
Ah! OK, great. Good luck!

theschweizer, 2015-05-26:
Thank you.
On May 26, 2015 10:49 AM, "Andrew Greenberg" <notifications@github.com>
wrote:

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

Closed 2016-05-19.

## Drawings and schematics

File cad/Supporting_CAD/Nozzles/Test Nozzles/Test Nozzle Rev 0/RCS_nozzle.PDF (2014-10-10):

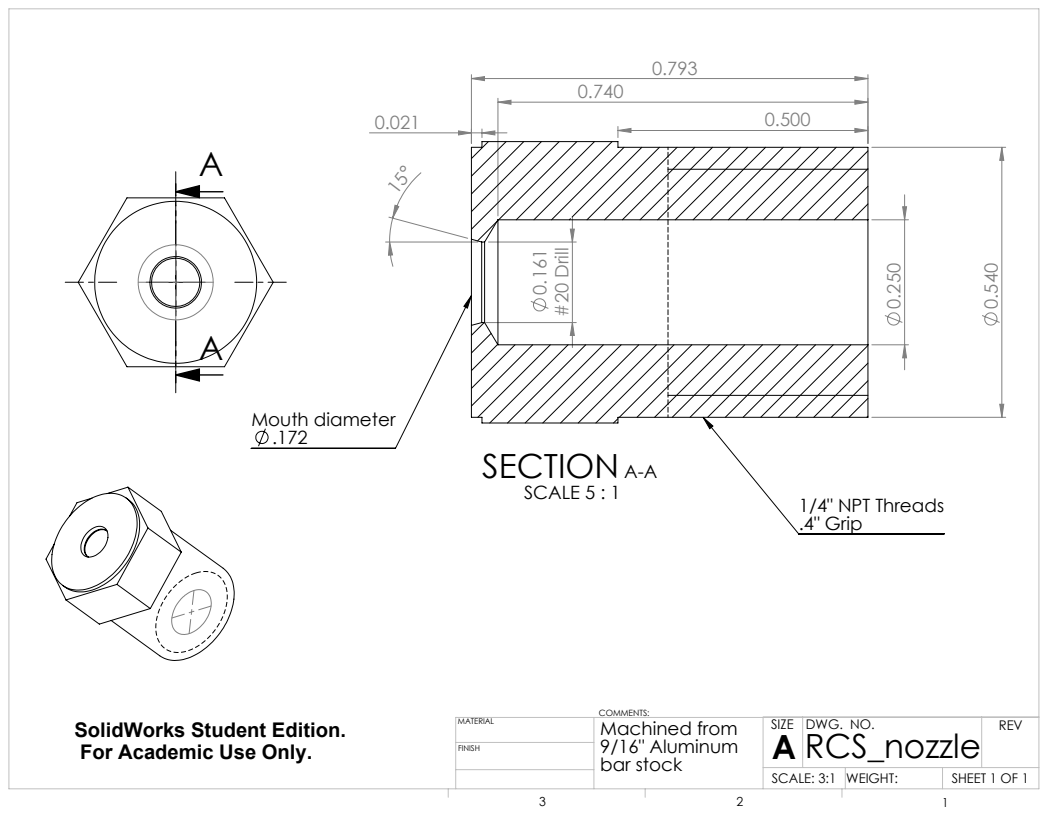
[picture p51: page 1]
#20 Drill; SECTION A-A SCALE 5 : 1; Mouth diameter; 1/4" NPT Threads .4" Grip; Machined from 9/16" Aluminum; bar stock; RCS_nozzle; SCALE: 3:1; WEIGHT:; SHEET 1 OF 1; DWG. NO.; REV

SolidWorks Student Edition.
For Academic Use Only.

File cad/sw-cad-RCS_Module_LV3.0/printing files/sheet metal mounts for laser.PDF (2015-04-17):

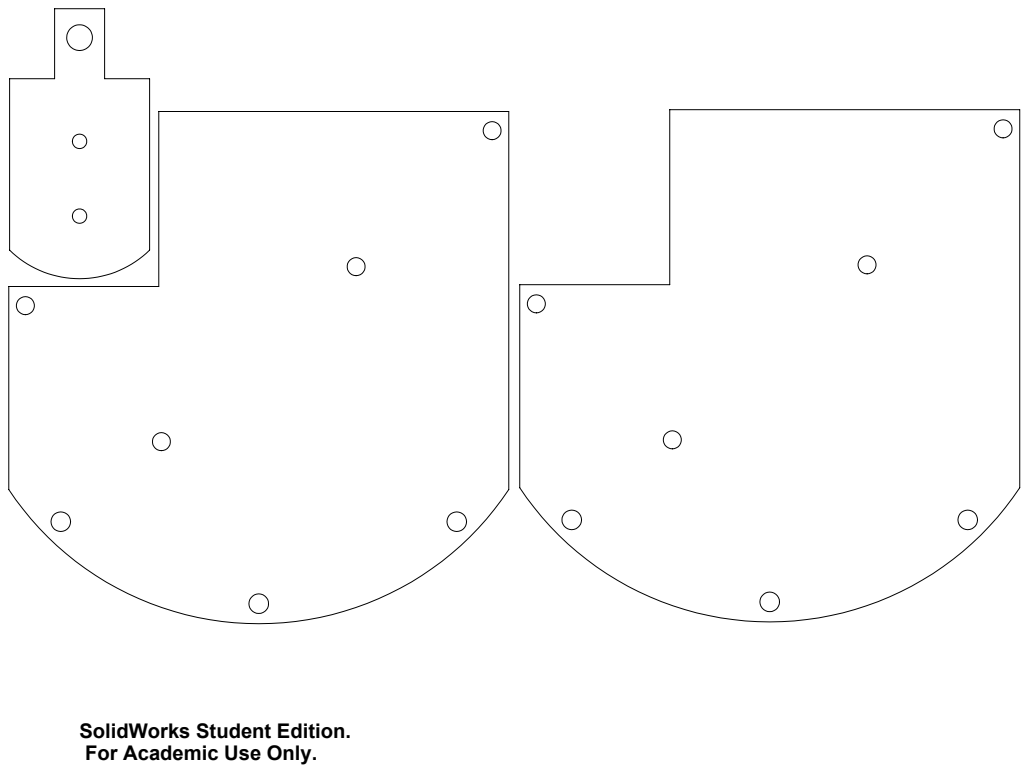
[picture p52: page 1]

SolidWorks Student Edition.
For Academic Use Only.

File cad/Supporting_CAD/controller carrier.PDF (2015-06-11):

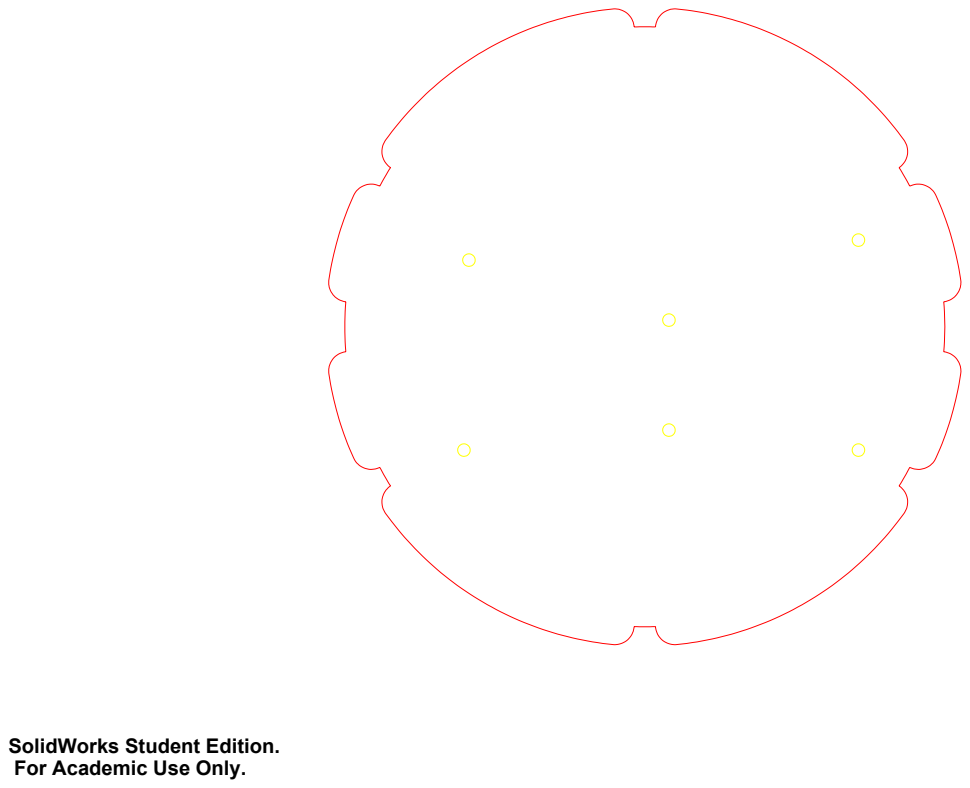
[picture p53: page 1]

SolidWorks Student Edition.
For Academic Use Only.

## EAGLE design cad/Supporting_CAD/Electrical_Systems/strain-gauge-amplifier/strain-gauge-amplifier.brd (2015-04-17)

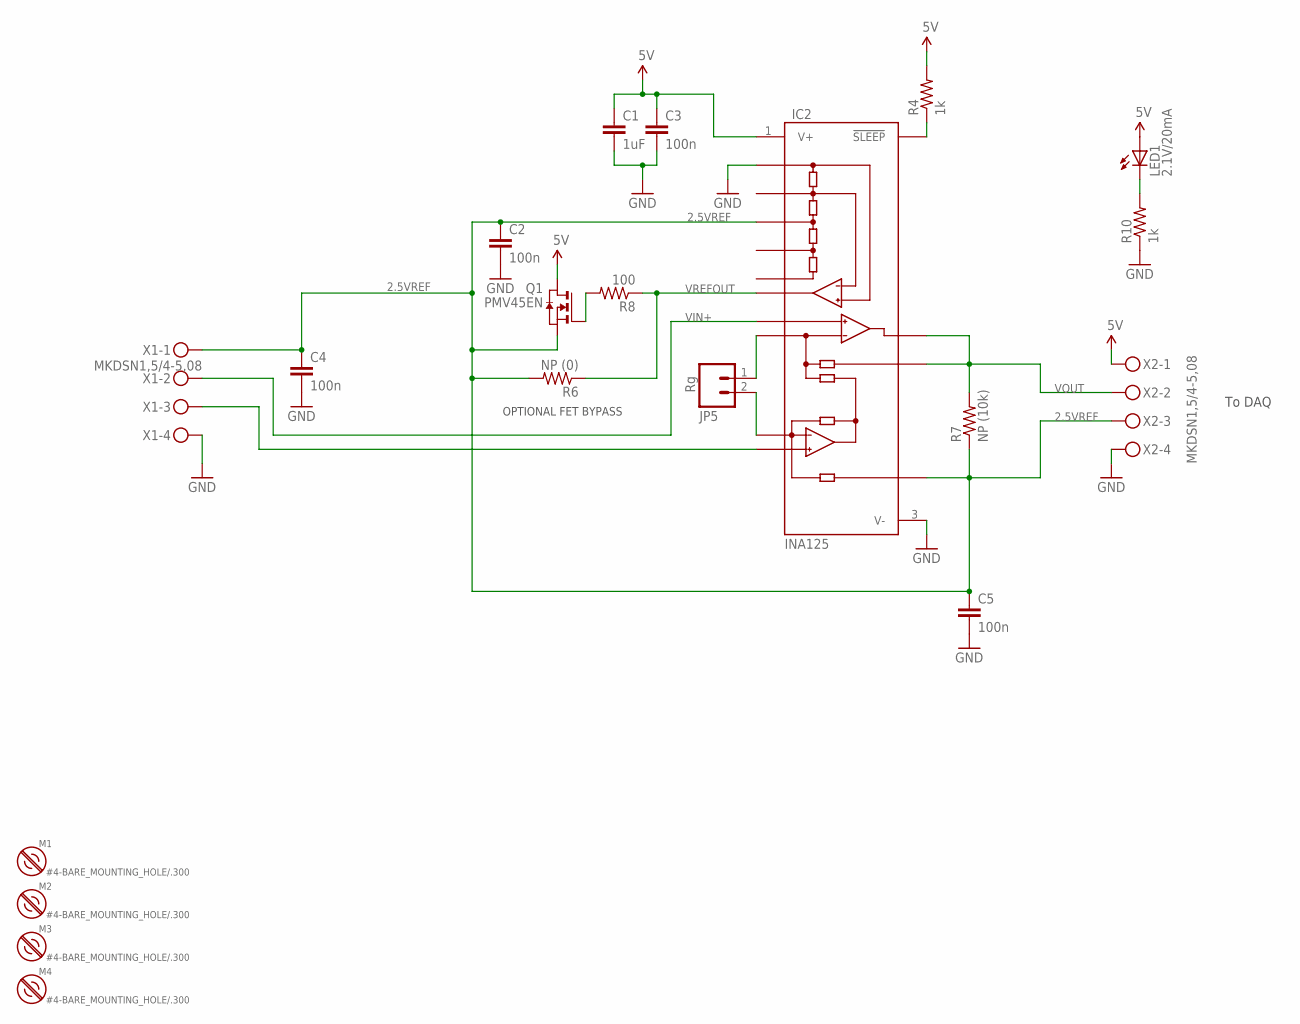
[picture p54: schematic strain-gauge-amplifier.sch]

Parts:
C1: 1uF; 0805-C-NOSILK
C2, C3, C4, C5: 100n; 0805-C-NOSILK
IC2: INA125; SO16
JP5: Rg; SCREWTERMINAL-5MM-2
LED1: 2.1V/20mA; LED-0603
M1, M2, M3, M4: #4-BARE_MOUNTING_HOLE/.300; #4/.300-BARE+STD_NUT_OR_STAR_WASHER
Q1: PMV45EN; SOT23
R4, R10: 1k; 0805-C-NOSILK
R6: NP (0); 0805-C-NOSILK
R7: NP (10k); 0805-C-NOSILK
R8: 100; 0805-C-NOSILK
X1, X2: MKDSN1,5/4-5,08

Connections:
2.5VREF: C2.1, C4.1, C5.1, IC2.5 (REF), IC2.14 (REF2.5), Q1.2 (S), R6.2, R7.1, X1.1, X2.3
5V: C1.1, C3.1, IC2.1 (V+), LED1.A, Q1.3 (D), R4.2, X2.1
GND: C1.2, C2.2, C3.2, C4.2, C5.2, IC2.3 (V-), IC2.12 (REFCOM), R10.1, X1.4, X2.4
unnamed: IC2.7 (-VIN), X1.3
unnamed: IC2.9 (RG), JP5.1
unnamed: IC2.8 (RG), JP5.2
unnamed: Q1.1 (G), R8.2
unnamed: IC2.2 (!SLEEP), R4.1
unnamed: LED1.C, R10.2
VIN+: IC2.6 (+IN), X1.2
VOUT: IC2.10 (OUT), IC2.11 (SENSE), R7.2, X2.2
VREFOUT: IC2.4 (REFOUT), R6.1, R8.1

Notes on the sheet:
OPTIONAL FET BYPASS
To DAQ

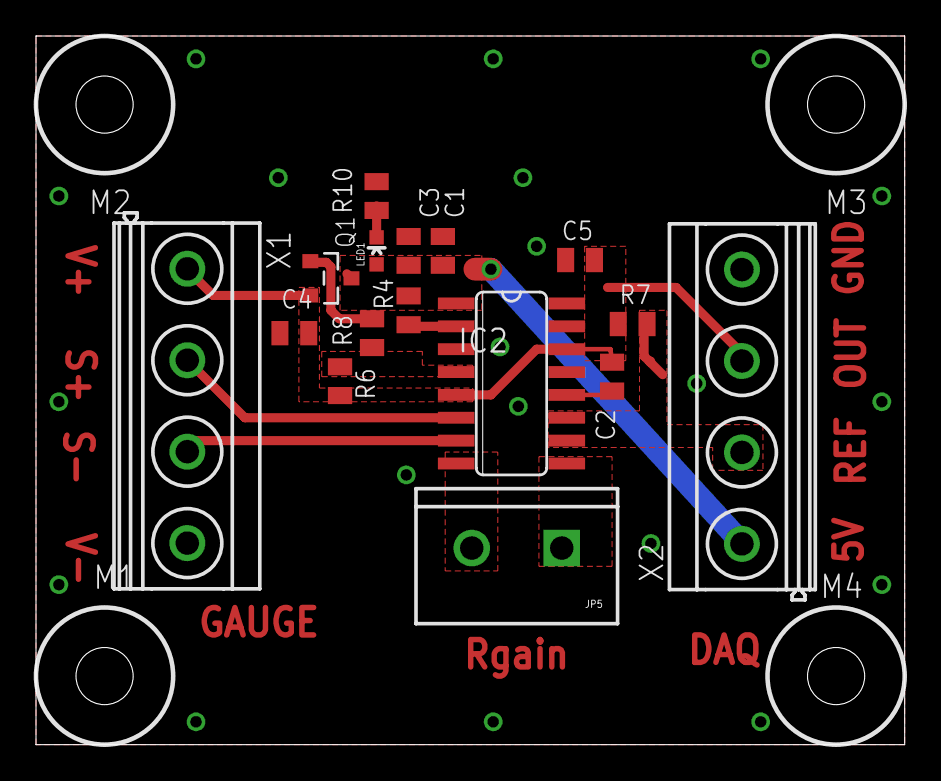
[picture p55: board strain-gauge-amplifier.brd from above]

Board: 2 copper layers, 48.3 x 39.4 mm, 20 parts (0 on the bottom side), 12 nets.

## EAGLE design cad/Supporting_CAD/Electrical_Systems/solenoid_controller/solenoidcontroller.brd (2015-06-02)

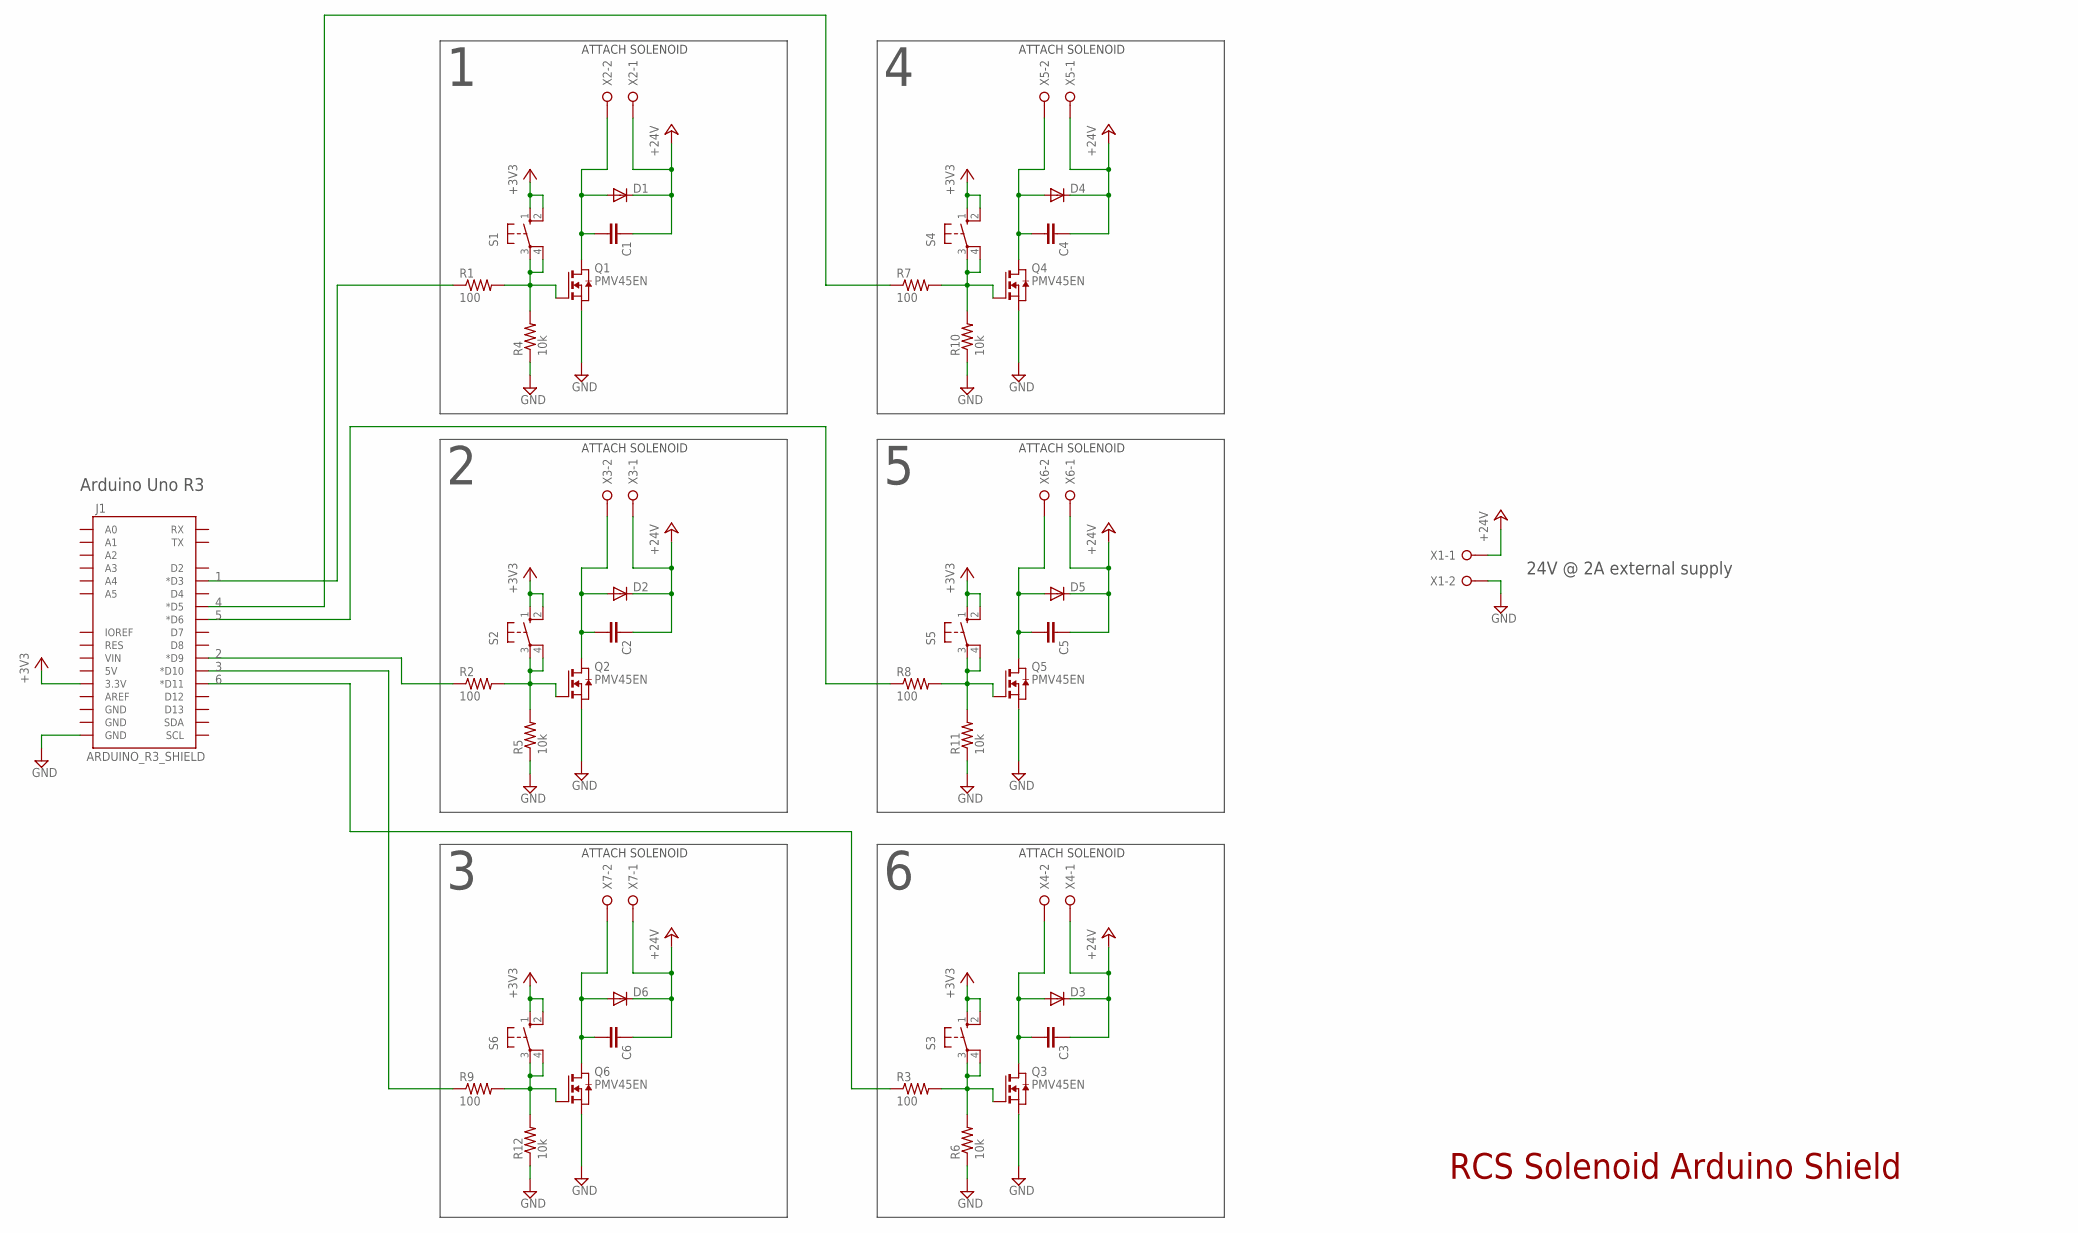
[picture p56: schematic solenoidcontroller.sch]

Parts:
C1, C2, C3, C4, C5, C6: C-EUC0603; C0603
D1, D2, D3, D4, D5, D6: DIODE-DO214BA; DO214BA
J1: ARDUINO_R3_SHIELD; UNO_R3_SHIELD
Q1, Q2, Q3, Q4, Q5, Q6: PMV45EN; SOT23
R1, R2, R3, R7, R8, R9: 100; R0603
R4, R5, R6, R10, R11, R12: 10k; R0603
S1, S2, S3, S4, S5, S6: 10-XX; B3F-10XX
X1, X2, X3, X4, X5, X6, X7: W237-02P; W237-132

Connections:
1: J1.D3 (*D3), R1.1
2: J1.D9 (*D9), R2.1
3: J1.D10 (*D10), R9.1
4: J1.D5 (*D5), R7.1
5: J1.D6 (*D6), R8.1
6: J1.D11 (*D11), R3.1
+3V3: J1.3.3V, S1.1 (S), S1.2 (S1), S2.1 (S), S2.2 (S1), S3.1 (S), S3.2 (S1), S4.1 (S), S4.2 (S1), S5.1 (S), S5.2 (S1), S6.1 (S), S6.2 (S1)
+24V: C1.1, C2.1, C3.1, C4.1, C5.1, C6.1, D1.C, D2.C, D3.C, D4.C, D5.C, D6.C, X1.1, X2.1, X3.1, X4.1, X5.1, X6.1, X7.1
GND: J1.GND@0 (GND), Q1.2 (S), Q2.2 (S), Q3.2 (S), Q4.2 (S), Q5.2 (S), Q6.2 (S), R4.1, R5.1, R6.1, R10.1, R11.1, R12.1, X1.2
unnamed: Q2.1 (G), R2.2, R5.2, S2.3, S2.4 (P1)
unnamed: Q3.1 (G), R3.2, R6.2, S3.3, S3.4 (P1)
unnamed: C2.2, D2.A, Q2.3 (D), X3.2
unnamed: C3.2, D3.A, Q3.3 (D), X4.2
unnamed: Q1.1 (G), R1.2, R4.2, S1.3, S1.4 (P1)
unnamed: C1.2, D1.A, Q1.3 (D), X2.2
unnamed: Q4.1 (G), R7.2, R10.2, S4.3, S4.4 (P1)
unnamed: C4.2, D4.A, Q4.3 (D), X5.2
unnamed: Q5.1 (G), R8.2, R11.2, S5.3, S5.4 (P1)
unnamed: C5.2, D5.A, Q5.3 (D), X6.2
unnamed: Q6.1 (G), R9.2, R12.2, S6.3, S6.4 (P1)
unnamed: C6.2, D6.A, Q6.3 (D), X7.2

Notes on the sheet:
ATTACH SOLENOID
24V @ 2A external supply
Arduino Uno R3
RCS Solenoid Arduino Shield

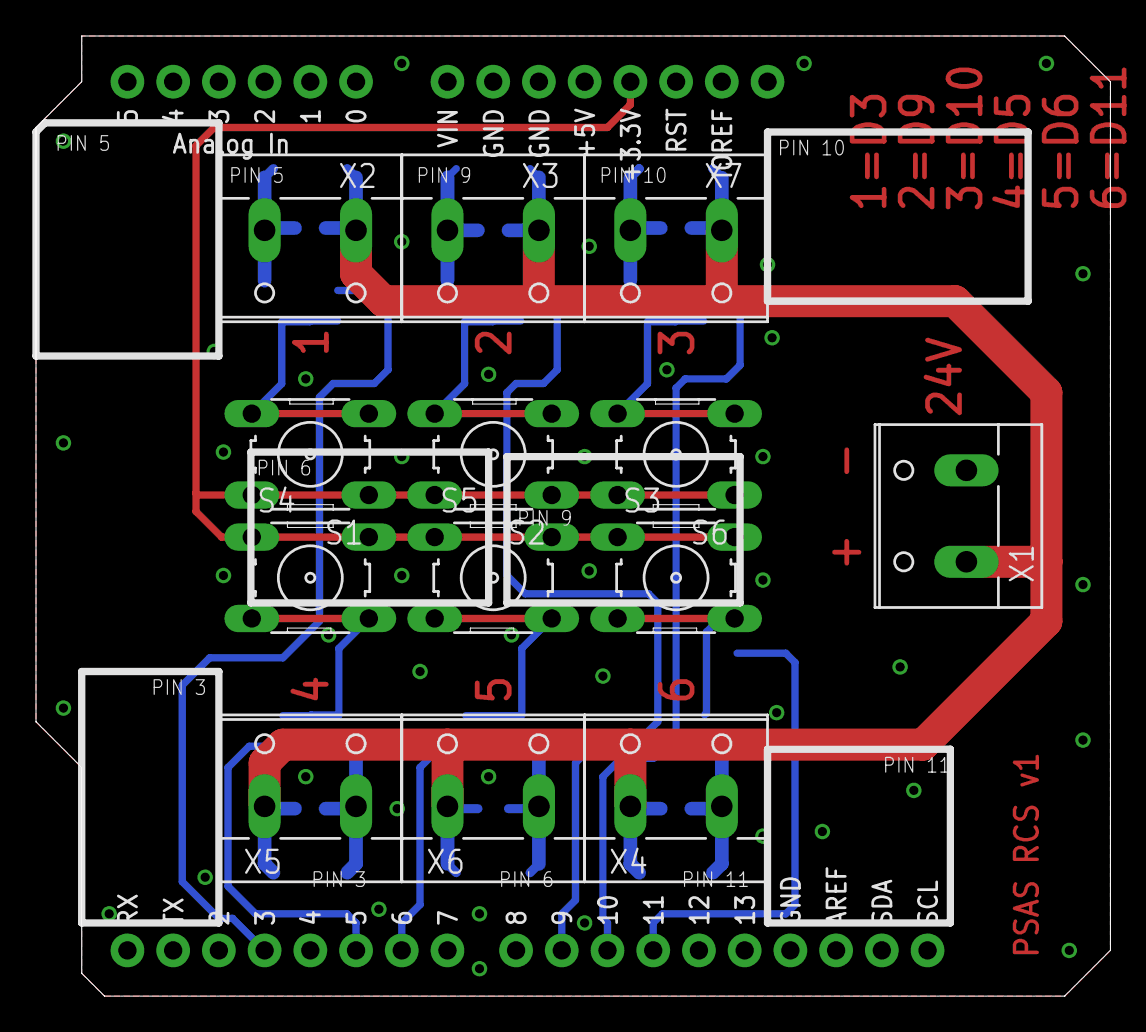
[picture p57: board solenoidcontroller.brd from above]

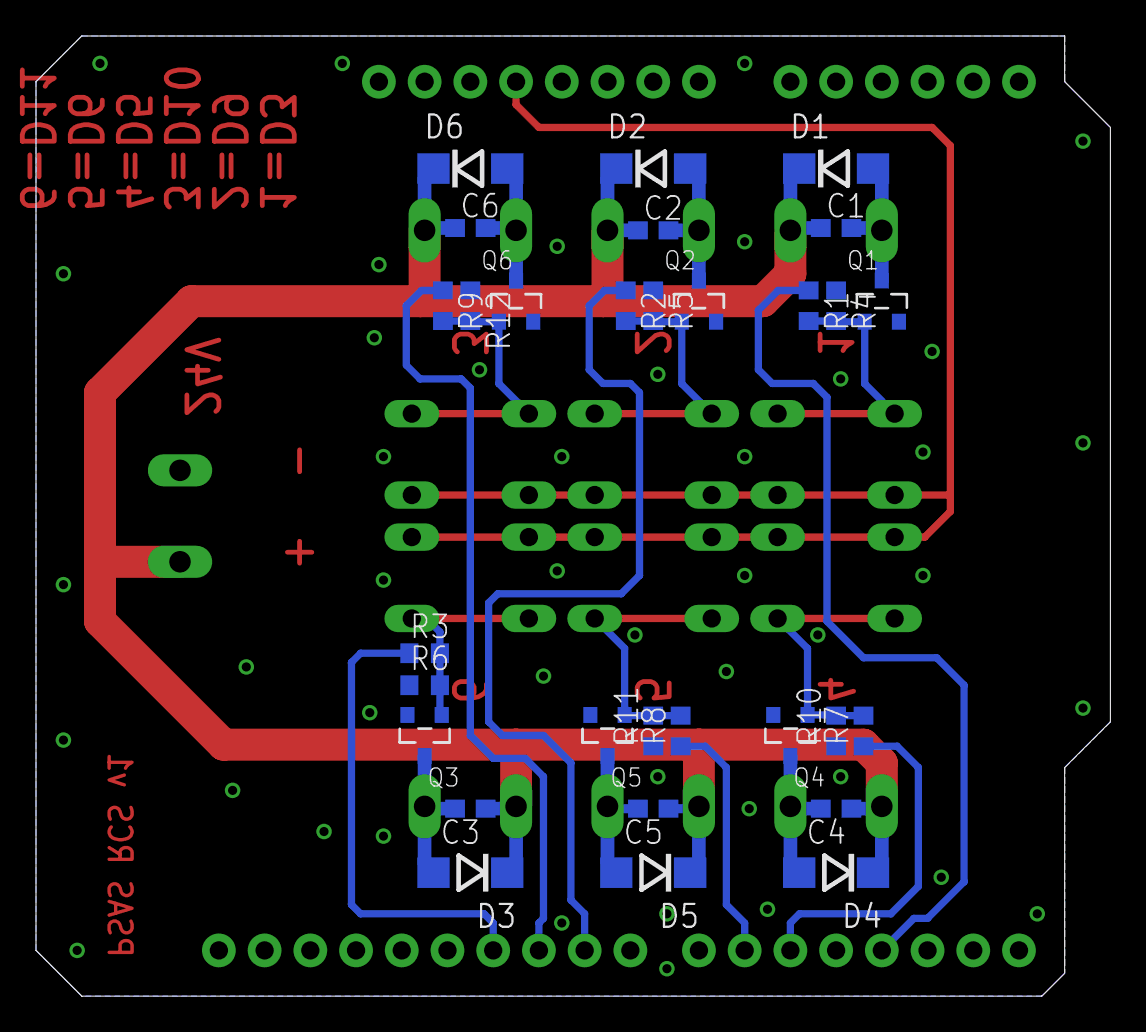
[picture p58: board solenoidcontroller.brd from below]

Board: 2 copper layers, 59.7 x 53.3 mm, 44 parts (30 on the bottom side), 21 nets.

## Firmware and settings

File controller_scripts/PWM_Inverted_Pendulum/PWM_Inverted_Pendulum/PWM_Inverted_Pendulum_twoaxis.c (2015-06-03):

/*
 * PWM_Inverted_Pendulum.c
 *
 * Created: 5/22/2015 4:27:00 PM
 *  Author: Robert Schweizer
  
 This program is being built to control the Pitch and Yaw dynamics of an rocket via an inverted pendulum simulation 
  
 */ 


#include <stdio.h>
#include <avr/io.h>
#include <avr/interrupt.h>
// Math functions
#include <math.h>
#include <stdlib.h>
#include <util/twi.h>



#define F_CPU 1000000UL // 1 MHz CPU Clock Frequency
#include <util/delay.h>

#include "mpu6050.h"

#define sbi(var, mask) ((var) |= (uint8_t)(1 << mask))
#define cbi(var, mask) ((var) &= (uint8_t)~(1 << mask))

volatile uint8_t buffer[14];

#define MPU6050_AXGAIN 16384.0
#define MPU6050_AYGAIN 16384.0
#define MPU6050_AZGAIN 16384.0

#define MPU6050_GXGAIN 131.0
#define MPU6050_GYGAIN 131.0
#define MPU6050_GZGAIN 131.0


// USART definitions
#define FOSC F_CPU  // CPU Clock Frequency must be set correctly for the USART to work
#define BAUD 4800
#define MYUBRR FOSC/16/BAUD-1

// USART declarations
static int    uart_putchar(char c, FILE *stream);
unsigned char uart_getchar(void);
static FILE mystdout = FDEV_SETUP_STREAM(uart_putchar, NULL, _FDEV_SETUP_WRITE);


int16_t		ax,           //Linear acceleration in the X direction (Raw Data)
			ay,           //Linear acceleration in the Y direction (Raw Data)
			az,           //Linear acceleration in the Z direction (Raw Data)
			gx,           //Angular Velocity about the X direction (Raw Data)
			gy,           //Angular Velocity about the Y direction (Raw Data)
			gz,           //Angular Velocity about the Z direction (Raw Data)
			//Tmp,           //Temperature reading
			d = 0;
double
			aXg,
			aYg,
			aZg,
			gXds,
			gYds,
			gZds,
			Xgyro,
			Ygyro,
			Zgyro,
			Yacc,
			Xacc,
			Zacc,
			AngleX = 0, AngleX_shift,
			AngleY = 0, AngleY_shift,
			AngleZ = 0, AngleX_shift,
			ErrorX,
			ErrorX_m1,
			ControlX,
			ControlX_m1;

int			PWM = 0,
			A = .758, 
			DT = .1667, 
			angle = 0,
			Kp = 1;


int main (void)
{
		//USART Setup
	UBRR0H = MYUBRR >> 8;
	UBRR0L = MYUBRR;
	UCSR0B = (1<<RXEN0)|(1<<TXEN0);
	stdout = &mystdout;                                          //Required for printf init

	DDRD=0b00000010;                                             //Set Output Port for USART
	
	
		// Initialize TWI/I2C
	
	mpu6050_init();

		/// Activate Output Pins
	DDRC |= (1 << 3)|(1 << 2)|(1 << 1)|(1 << 0);                 //activate a clock measurement pin for debugging

		//Port D Activat OC2B, OC0B, OC0A
	DDRD  |= (1 << PORTD3)|(1 << PORTD5)|(1 << PORTD6);          //set data direction 
	
		//Port B Activate OC1A, OC2A
	DDRB  |= (1 << PORTB1);//|(1 << PORTB3);                        //set data direction 



	PORTD |= (0 << PORTD3)|(0 << PORTD5)|(0 << PORTD6);                        //activate pins
	PORTB |= (0 << PORTB1)|(0 << PORTB3);                        //activate pins
 

		// Interrupt Timer to Timer 1 (16-bit resolution)

	TCCR1A |= (1 << COM1A1);                                     // OC1n clears on compare match (non-inverting PWM mode)
	TCCR1B |= (1 << WGM12);                                      // sets CTC mode to using OCR1nA as TOP of counter
	TIMSK1 |= (1 << OCIE1A);                                     // Enable CTC interrupt
	
	
	TCCR1B |=(1 << CS10)|(0 << CS11)|(1 << CS12);                // sets the prescaler on the clock frequency to 1024
	
		////  TARGET FREQUENCY CALCULATION ////////////////////
		////  Target Frequency =  F CPU/(2*Prescale*(OCR1A+1)) 
	
	OCR1A = 120;                                                  //This sets frequency of interrupt to about 6 Hz
	sei();                                                       // Enable global interrupts
	
	// PWM Timer set to Timer 0 (8-bit resolution)  ** Timer 0 and Timer 1 share the set prescale value
	
	TCCR0A |= (1 << COM0A1)|(0 << COM0A0)|(1 << COM0B1)|(0 << COM0B0)|(1 << WGM00)|(1 << WGM01);   //Setting up Fast PWM with OCR0A and OCROB as compare registers
	TCCR0B |= (0 << WGM02)|(1 << CS02)|(0 << CS01)|(1 << CS00);                                    // Defines Fast PWM and activates timer
	
	//PRR |= (0 << PRTIM2)
	TCCR2A |= (1 << COM2A1)|(0 << COM2A0)|(1 << COM2B1)|(0 << COM2B0)|(1 << WGM20)|(1 << WGM21);   //Setting up Fast PWM with OCR0A and OCROB as compare registers
	TCCR2B |= (0 << WGM22)|(1 << CS22)|(1 << CS21)|(1 << CS20);
  
	while(1)
	{
		//d = OCR0A;
		//printf("TCNT2 %d;", d);
		mpu6050_getConvData(&aXg,&aYg,&aZg,&gXds,&gYds,&gZds);  //reads in accel and gyro data and apply sensitivity conversion and stores in addressed variables
		
		//printf("   %f;   %f;   %f;\n   %f;   %f;   %f;\n\n",aXg,aYg,aZg,gXds,gYds,gZds);
		//_delay_ms(150);
		
		// Integrating angular velocity to get the angle based on gryo data
		Xgyro = gXds*DT;
		Ygyro = gYds*DT;
		Zgyro = gZds*DT;
		
		//printf("\nangle X %f;  gXds %f;  Xacc %f;\n",X,gXds,Xacc);
		
		// Finding the angle based on accel data
		Xacc = atan2f(aYg,aZg)*180/M_PI;
		Yacc = atan2f(aXg,aZg)*180/M_PI;
		Zacc = atan2f(aXg,aYg)*180/M_PI;
		
		// Complimentary Fitler Equation   ** this is important to remove drift that is a symptom of only using the gyro for angle calculations
		AngleX = A * (AngleX + Xgyro) + (1-A) * Xacc;
		AngleY = A * (AngleY + Ygyro) + (1-A) * Yacc;
		AngleZ = A * (AngleZ + Zgyro) + (1-A) * Zacc;
		
		ErrorX = AngleX;
		ControlX = Kp*ErrorX;
		//ControlX = 1.114*ErrorX - 0.7727*ErrorX_m1 +ControlX_m1;
		ErrorX_m1 = ErrorX;
		ControlX_m1 = ControlX;
		
		//printf(" %f; \n\n",ControlX);
		
		// Determining with solenoid to actuate and the duty cycle to use.
		if (ControlX < -172 && -178.6 < ControlX )          //The system can only control from 1.4 to 8 degrees
		{
			AngleX_shift = ControlX + 180;
			PWM =( 0.6/6.6*AngleX_shift + .0727272)*256; //Relationship based off experimental data of duty cycle and thrust output
			OCR0A = PWM;
			printf("%d;  right     %f;\n", PWM,AngleX_shift);
			
			//return;
		}
		
	/*		
		else if(172 < ControlX && ControlX < 178.6)
		{
			AngleX_shift = 180 - ControlX;
			PWM =( 0.6/7.3*AngleX_shift + .06027397)*256; //Relationship based off experimental data of duty cycle and thrust output
			OCR0B = PWM;
			//printf("%d;   left     %f;\n", PWM,AngleX_shift);
			
			
			//return;
		}
		
		
		else if((ControlX < -178.6 || ControlX > 178.6)&&(ControlX > -172 || ControlX < 172));
		{
			//printf("working??\n");
			OCR0A = 0;
			OCR0B = 0;
			//return;
		}
	if (AngleY < -172 && -178.6 < AngleY)
	{
		AngleY_shift = AngleY + 180;
		PWM =( 0.6/6.6*AngleY_shift + .0727272)*256; //Relationship based off experimental data of duty cycle and thrust output
		OCR2A = PWM;
		printf("%d; back     %f;\n", PWM,AngleY_shift);
				
		return;
	}
			else if(172 < AngleY && AngleY < 178.6)
			{
				AngleY_shift = 180 - AngleY;
				PWM =( 0.6/7.3*AngleY_shift + .06027397)*256; //Relationship based off experimental data of duty cycle and thrust output
				OCR2B = PWM;
				printf("%d;   front     %f;\n", PWM,AngleY_shift);
				
				
				return;
			}
			else if((AngleY< -178.6 || AngleY > 178.6)&&(AngleY > -172 || AngleY < 172));
			{
				printf("2working??\n");
				OCR2A = 0;
				OCR2B = 0;
				return;
			}*/
		}
	
	
}

ISR(TIMER1_COMPA_vect)                                      //runs an interrupt comparing timer to OCR1A
{
	PORTC ^= (1 << 0);                                    // Debug toggle switch for interupt frequency check
/*
	mpu6050_getConvData(&aXg,&aYg,&aZg,&gXds,&gYds,&gZds);  //reads in accel and gyro data and apply sensitivity conversion and stores in addressed variables
	
			//printf("   %f;   %f;   %f;\n   %f;   %f;   %f;\n\n",aXg,aYg,aZg,gXds,gYds,gZds);
			//_delay_ms(150);
	
	// Integrating angular velocity to get the angle based on gryo data
	Xgyro = gXds*DT;              
	Ygyro = gYds*DT;
	Zgyro = gZds*DT;
	
				//printf("\nangle X %f;  gXds %f;  Xacc %f;\n",X,gXds,Xacc);
	
	// Finding the angle based on accel data
	Xacc = atan2f(aYg,aZg)*180/M_PI;
	Yacc = atan2f(aXg,aZg)*180/M_PI;
	Zacc = atan2f(aXg,aYg)*180/M_PI;
	
	// Complimentary Fitler Equation   ** this is important to remove drift that is a symptom of only using the gyro for angle calculations
	AngleX = A * (AngleX + Xgyro) + (1-A) * Xacc;
	AngleY = A * (AngleY + Ygyro) + (1-A) * Yacc;
	AngleZ = A * (AngleZ + Zgyro) + (1-A) * Zacc;
	
	ErrorX = AngleX; 
	ControlX = Kp*ErrorX;
	//ControlX = 1.114*ErrorX - 0.7727*ErrorX_m1 +ControlX_m1;
	ErrorX_m1 = ErrorX;
	ControlX_m1 = ControlX;
	
				//printf(" %f; \n\n",ControlX);
	
	// Determining with solenoid to actuate and the duty cycle to use.
	if (ControlX < -172 && -178.6 < ControlX )          //The system can only control from 1.4 to 8 degrees
	{
		AngleX_shift = ControlX + 180;
		PWM =( 0.6/6.6*AngleX_shift + .0727272)*256; //Relationship based off experimental data of duty cycle and thrust output
		OCR0A = PWM;
		printf("%d;  right     %f;\n", PWM,AngleX_shift);
		
		//return;
	}
	
	
		else if(172 < ControlX && ControlX < 178.6)
		{
			AngleX_shift = 180 - ControlX;
			PWM =( 0.6/7.3*AngleX_shift + .06027397)*256; //Relationship based off experimental data of duty cycle and thrust output
			OCR0B = PWM;
			//printf("%d;   left     %f;\n", PWM,AngleX_shift);
			
		
			//return;
		}
		
		
			else if((ControlX < -178.6 || ControlX > 178.6)&&(ControlX > -172 || ControlX < 172));
			{
				//printf("working??\n");
				OCR0A = 0;
				OCR0B = 0;
				return;
				
	if (AngleY < -172 && -178.6 < AngleY)
	{
		AngleY_shift = AngleY + 180;
		PWM =( 0.6/6.6*AngleY_shift + .0727272)*256; //Relationship based off experimental data of duty cycle and thrust output
		OCR2A = PWM;
		printf("%d; back     %f;\n", PWM,AngleY_shift);
	
		return;
	}
		else if(172 < AngleY && AngleY < 178.6)
		{
			AngleY_shift = 180 - AngleY;
			PWM =( 0.6/7.3*AngleY_shift + .06027397)*256; //Relationship based off experimental data of duty cycle and thrust output
			OCR2B = PWM;
			printf("%d;   front     %f;\n", PWM,AngleY_shift);
	
	
			return;
		}
			else if((AngleY< -178.6 || AngleY > 178.6)&&(AngleY > -172 || AngleY < 172));
			{
				printf("2working??\n");
				OCR2A = 0;
				OCR2B = 0;
				return;
			}	
	}*/
}


// USART Functions

static int uart_putchar(char c, FILE *stream)
{
	if (c == '\n') uart_putchar('\r', stream);
	
	loop_until_bit_is_set(UCSR0A, UDRE0);
	UDR0 = c;
	
	return 0;
}

unsigned char uart_getchar(void)
{
	while( !(UCSR0A & (1<<RXC0)) );
	return(UDR0);
}

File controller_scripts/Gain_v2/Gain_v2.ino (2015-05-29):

#include <Wire.h>

#define A_GAIN 0.932    // [deg/LSB]
#define G_GAIN 1.466    // [deg/s/LSB]

#define DT 0.002         // [s/loop] loop period
#define A 0.98         // complementary filter constant

#define KP 1.8          // proportional controller gain [LSB/deg/loop]
#define KD 0.4          // derivative controller gain [LSB/deg/loop]
#define KI 0.5          // Integral controller gain

float accel = 0.0;
float angle = 0.0;      // [deg]
float rate = 0.0;       // [deg/s]
float output = 0.0;     // [LSB] (100% voltage to motor is 255LSB)

float accelX = 0.0;
float angleX = 0.0;      // [deg]
float rateX = 0.0;       // [deg/s]
float rateXrad = 0.0;     // [rad/s]
float rateXave = 0.0;     // [deg/s]
float outputX = 0.0;     // [LSB] (100% voltage to motor is 255LSB)

float accelY = 0.0;
float angleY = 0.0;      // [deg]
float rateY = 0.0;       // [deg/s]
float outputY = 0.0;     // [LSB] (100% voltage to motor is 255LSB)

float rateZ = 0.0;       // [deg/s]

#define num  1      // for smoother
int reader[num];         // for smoother
int Index = 0;           // for smoother
float total = 0.0;         // for smoother
float ave = 0.0;           // ave the rate for smoother
float rateD = 0.00;      // desired roll rate
#define kp 0.41            // proportional gain for duty cycle
float a = 1.0 * kp;        // (I/(r*.1s))/Ftot equation to dc from radian error
float u = 0.0;
float aveRad = 0.0;


const int MPU=0x68;  // I2C address of the MPU-6050
float AcX;
float AcY;
float AcZ;
float GyX;
float GyY;
float GyZ;
float Tmp;
float d = 0;

#define onTime 200
unsigned long previousMillis = 0;        // will store last time LED was updated
int interval = onTime;
boolean ledState = LOW;                 // ledState used to set the LED
//const long interval = 100;             // interval at which to blink (milliseconds)
#define MPU6050_DLPF_CFG3     6          //Built in low pass filter section delay 4.9ms
#define MPU6050_CONFIG       0x1A        //congfig register for MPU6050

#define cw  3
#define ccw  5

void setup() {
  
  Wire.begin();
  Wire.beginTransmission(MPU);
  Wire.write(0x6B);            // PWR_MGMT_1 register
  Wire.write(0);               // set to zero (wakes up the MPU-6050)      
  Wire.endTransmission(true);
  Wire.beginTransmission(MPU);
  Wire.write(MPU6050_CONFIG);  // digital filter resgister fs 1 Khz
  Wire.write(MPU6050_DLPF_CFG3);     // set to zero (wakes up the MPU-6050)      
  Wire.endTransmission(true);
  pinMode(cw, OUTPUT);
  pinMode(ccw, OUTPUT);
  pinMode(A0, INPUT);
  Serial.begin(9600);
  digitalWrite(ccw, LOW);
  digitalWrite(cw, LOW);
  for (int i = 0; i < num; i++)
    reader[i] = 0;
  delay(1000);
  
}

void loop(){
  if (millis() < 15000){

      IMU(); //call IMU function
      
      if (aveRad >= 0.08) {
        blinkwd();
        digitalWrite(cw,ledState);
      }
      
      //acvitate solenoids to roll counter-clockwise  
      else if (aveRad <= -0.08) {
        blinkwd();
        digitalWrite(ccw,ledState);
      }
      
      //sweetspot!! no roll action to solenoids
      else {
        digitalWrite(cw,LOW);
        digitalWrite(ccw,LOW);    
      }


 
      delay(1);
  }
  
 else{
    digitalWrite(cw,LOW);
    digitalWrite(ccw,LOW);
  }
 
  /*
  Serial.print(" | rateXaveRad = ");
  Serial.println(aveRad);
  Serial.print(" | rateX = ");
  Serial.print(rateX);
  Serial.print("   |ledstate   ");
  Serial.print(ledState);
  Serial.print("   |u   ");
  Serial.print(u);
  */
  
  
}


void blinkwd(){
  IMU();
  u = a*abs(aveRad);
  unsigned long currentMillis = millis(); 
  
  if (u >= 1){
    ledState = HIGH; 
  }
  
  else if (abs(u) < .075 ){  
    ledState = LOW;      
  
  }
 
  
  else if ((unsigned long)(currentMillis - previousMillis) >= interval) {
    
    if (ledState) {
      interval = onTime-u*onTime;
    } 
    
    else {
      interval = u*onTime;
    }
    ledState = !(ledState);
    previousMillis = currentMillis;
  }
  

}

void IMU(){ //IMU function for MPU-6050 
  Wire.beginTransmission(MPU);
  Wire.write(0x3B);  // starting with register 0x3B (ACCEL_XOUT_H)
  Wire.endTransmission(false);
  Wire.requestFrom(MPU,14,true);
  AcX=Wire.read()<<8|Wire.read();
  AcY=Wire.read()<<8|Wire.read(); 
  AcZ=Wire.read()<<8|Wire.read(); 
  Tmp=Wire.read()<<8|Wire.read(); 
  GyX=Wire.read()<<8|Wire.read(); 
  GyY=Wire.read()<<8|Wire.read(); 
  GyZ=Wire.read()<<8|Wire.read();
  ////////////////////////////////////////////////////////////
  //output for Pitch tilt
  rateX = GyX / 131;//7528 for rad or / by 131 for deg
//  Serial.print(" | rateX = ");
//  Serial.println(rateX);
/*
  //set accell rate
  accelY = AcY / 16384;
  Serial.print(" | accY = ");
  Serial.print(accelY);
  //determine the angle
  angleX = A * (angle + rate * DT) + (1 - A) * accel;  
  Serial.print(" | angX = ");
  Serial.print(angleX);
  //set the scalar reaction 
  outputX = (angle * KP + rate * KD) ;
  Serial.print(" | outX = ");
  Serial.print(outputX);
  ////////////////////////////////////////////////////////////
  //output for Yaw tilt
 
  rateY = GyY / 131;  
  Serial.print(" | rateY = ");
  Serial.print(rateY);
 
  //set accell rate
  accelX = AcX / 16384;
  Serial.print(" | accX = ");
  Serial.print(accelX);
  //determine the angle
  angleY = A * (angle + rate * DT) + (1 - A) * accel;  
  Serial.print(" | angY = ");
  Serial.print(angleY);
  //set the scalar reaction 
  outputY = (angle * KP + rate * KD) ;
  Serial.print(" | outY = ");
  Serial.print(outputY);
  ////////////////////////////////////////////////////////////
  //output for roll rate
  rateZ = GyZ / 131;  
  Serial.print(" | rateZ = ");
  Serial.println(rateZ);
  */
  total = total - reader[Index];
  reader[Index] = rateX;
  total = total + reader[Index];
  Index = Index + 1; 
  if (Index >= num)
    Index = 0;
    
  ave = total /num;
  
  aveRad = ave/57.3;
//  Serial.print(" | rateXaveRad = ");
//  Serial.println(aveRad);  
}

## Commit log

2014-10-10 Sea Level test nozzle CAD and drawings
    [RCS_nozzle.SLDDRW, RCS_nozzle.SLDPRT]
2014-10-25 first attempt at a complete module for the RCS
    [.125 NPT Nipple.SLDPRT, .125 NPT quick disconnect.SLDPRT, .25 NPT Nipple.SLDPRT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]
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2014-12-17 nevermind
    I don't want those crappy .sdlprt files any ways
    [deLaval cutaway.SLDPRT, deLaval.SLDPRT, half cone e-15.SLDPRT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]
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2015-01-20 Revert "nevermind"
    This reverts commit 430d1ab73a2580e48ba750538cf57433fbc770e6.
    Conflicts:
    3d Printing nozzles/deLaval.SLDPRT
    [deLaval cutaway.SLDPRT, deLaval.SLDPRT, half cone e-21.SLDPRT]
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2015-03-02 Update RCS_thermoDYNAMICS.m
    Automatically calculated initial conditions, corrected mass flow rate relation, corrected solenoid Cv relation.
2015-03-04 updates and old versions of nozzle ring
    has new designs of the nozzles (pitch and roll are combined to one
    printed part)
    [2227K110.SLDPRT, 53415K202.SLDPRT, 5463K248.SLDPRT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]
2015-03-05 working on combined nozzles with scarfing calculations
    [roll and pitch coupled nozzles v2.SLDPRT, roll and pitch coupled nozzles.SLDPRT]
2015-03-05 added equations that give the effective expansion ratio of the scarfed nozzles
    [half cone e-15.SLDPRT, roll and pitch coupled nozzles v2.SLDPRT]
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2015-03-07 started drawing for nozzle ring
    [Nozzle carrying ring (3_4_15).SLDDRW, Nozzle carrying ring (3_4_15).SLDPRT]
2015-03-10 added first test of single stream
    [Full open.xlsx, Pulse 60ms.xlsx, Sensor Calibration.xlsx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]
2015-03-11 added new test data
    [300psi_100ms2015-03-10 17-13.xlsx, 300psi_tank_drain_950psi_start2015-03-10 17-24.xlsx, Dry_run_solenoid 15ms.xlsx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]
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2015-03-12 added second test session data
    [Temp_cal.xlsx]
2015-03-13 added calibrated data to the excel files
    [Calibrations.xlsx, Pressure_cal.xlsx, Sensor Calibration.xlsx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]
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2015-03-13 fixed calibrations
    [Calibrations.xlsx, wet run 120 ms with 50 percent duty cycle2015-03-12 14-37.xlsx, wet run 200 ms with 30 percent duty cycle2015-03-12 14-25.xlsx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]
2015-03-13 checking interference in the pressure sensor data
    [Calibrations.xlsx, wet run 120 ms with 50 percent duty cycle2015-03-12 14-37.xlsx, wet run 200 ms with 50 percent duty cycle2015-03-12 14-28.xlsx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]
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2015-03-15 added graphs for data
    [Calibrations.xlsx, Full open.xlsx, full open old solenoid.xlsx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]
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2015-03-21 single stream data for paper
    [Calibrations.xlsx]
2015-03-22 working on fitting everything into the module (stuff)
    added swagelock regulator, solenoids, tube fittings, etc
    [4082T420.SLDPRT, Air_Tank (Luxfer L17D 150ci).SLDPRT, Air_Tank.SLDPRT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]
2015-03-23 I don't remember what I was doing... oh well
    [Module_ASSY.SLDASM, Tube_1-nozzle ring v2.sldasm, Tube_1-solenoid with fittings.sldasm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]
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2015-03-23 adding tubing to the drawings
    fyi the solidworks tube routing add-on is a piece of garbage
    [Module_ASSY.SLDASM, Tube_1-nozzle ring v2.sldasm, Tube_11-nozzle ring v2.sldasm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]
2015-03-24 stuffy stuff from meeting
    [Carbon motor module Sleeve.SLDPRT, High Pressure Assembly (3-21-15).SLDASM, Module_ASSY.SLDASM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]
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2015-03-30 Update RCS_Arduino_controller__BANG__.ino
    fixed the negatives issue
    [RCS_Arduino_controller__BANG__.ino]
2015-03-30 fixed rates for correct coordinates
    [RCS_Arduino_controller__BANG__.ino]
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2015-04-01 removed outdated solidworks files
    and rearranged some stuff
    [.125 NPT Nipple.SLDPRT, .125 NPT quick disconnect.SLDPRT, .25 NPT Nipple.SLDPRT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]
2015-04-01 stuff and things (nothing was actually changed)
    [Module_ASSY.SLDASM, Tube_1-nozzle ring v2.sldasm, Tube_1-solenoid with fittings-001.sldasm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]
2015-04-02 modified the solenoids
    added a chamfer that is .3 in x .152 in
    [FCR 6in 4_6_14 Final.SLDPRT, FCR 6in Final.SLDPRT, Module_ASSY.SLDASM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]
2015-04-02 added deLaval geometry to all nozzles
    [FCR 6in 4_6_14 Final.SLDPRT, MCR 6in 4_6_14 Final.SLDPRT, MCR 6in Final.SLDPRT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]
2015-04-02 added new STL of the ring and more expansion ratios
    [deLaval pitch yaw (ER-2).STL, deLaval roll and pitch coupled nozzles.SLDPRT, nozzle ring v2.SLDASM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]
2015-04-03 adding part files for all of the expansion ratios
    [deLaval roll and pitch coupled nozzles (roll ER 2-5 Pitch ER 2).SLDPRT]
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2015-04-05 Added solenoid controller schematic and board
    [solenoidcontroller.brd, solenoidcontroller.sch]
2015-04-05 Cleaned up Baker's already A-OK board. Switched kickback components to bottom to minimimze copper length, fattened up power traces and reduced length, added text on top layer, re-numbered the solenoi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
    [solenoidcontroller.brd, solenoidcontroller.sch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]
2015-04-05 Updated solenoid controller board; moved all SMD components to bottom layer and power traces to top layer.
    [solenoidcontroller.brd, solenoidcontroller.sch]
2015-04-05 Generated new gerbers from Baker's commit.
    [solenoidcontroller.xln]
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2015-04-10 added solenoid bracing and fixed dependencies
    [48805K183.SLDPRT, 51205K112.SLDPRT, 51205K272.SLDPRT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]
2015-04-14 working on the solenoid bracket
    [Module_ASSY.SLDASM, Short Module.SLDASM, Solenoid bracket (left).SLDPRT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]
2015-04-15 started making ridgidity changes to solendoids
    started making manifold
    [Module_ASSY.SLDASM, Short Module.SLDASM, Solenoid bracket (left).SLDPRT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]
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2015-04-16 Old strain gauge amplifer from airframe project. Comitting just for safety.
    [strain-gauge-amplifier.brd, strain-gauge-amplifier.sch, strain-gauge-amplifier.xls]
2015-04-17 new straingauge board for 4 white strain gauge.
    [strain-gauge-amplifier.brd, strain-gauge-amplifier.sch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]
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2015-04-25 RCS with feed back and gain
    takes IMU data and converts error to duty cycle output, which can be
    directly proportional to thrust.
    [RCS_Roll_Feedback_Gain.ino]
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2015-04-28 Turns nozzle on for short duration after delay
    [FirstRollTest.ino]
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2015-05-13 inverted pendulum stand
    [1_5PVC 3way90deg.SLDPRT, 1_5PVC Tee.SLDPRT, 1_5PVC cross.SLDPRT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]
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2015-05-20 added some research for the new IMU
    and pin designations for edison mini break out
    [Module_ASSY.SLDASM, Tube_11-Tank Module Assembly.sldasm]
2015-05-25 ported Gain_v2 to python2.7 now called Gain_v3
    and added inso for the new IMU
    [Module_ASSY.SLDASM, Tube_11-Tank Module Assembly.sldasm]
2015-05-31 PWM Inverted Pendulum script
    updating changes
    [PWM_Inverted_Pendulum.c, mpu6050.h]
2015-05-31 Update Working code
    Timers are working correctly for PWM for Pitch only. Next step is
    implement a controller and then look at adding Yaw.
    [PWM_Inverted_Pendulum.c]
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2015-06-03 1 axis Inverted Pendulum Code v1.5
    [PWM_Inverted_Pendulum_Xmega.c, PWM_Inverted_Pendulum_twoaxis.c]
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2017-03-09 reorganization, and added a bunch of old files
    [.125 NPT quick disconnect.SLDPRT, .25 NPT Plug.SLDPRT, 1.csv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]
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2021-04-04 first draft of the flight fittings diagram
    There's a lot of missing info and conflicts.
    - The regulator is nickel-plated aluminum (6061). I think there's another plated component somewhere. Someone should look into the reliability of nickel plating in preventing corrosion.
    - The LPFlight relief valve (PRV-01) seems to be spec'd oddly. It uses a brass body instead of stainless and a Viton seal instead of Buna-N.
    - PRV-01 also uses a burst-disk symbol instead of a relief valve symbol. Since there seem to be different standards for this, I would like us to compile a short list of "RCS-canonical" symbols.
    - The HPFlight tank should have a more unique desgnator than just "N2". I propose "HPFT".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
2021-04-07 started diagrams for the fill and vent systems.
    Notes on fill system fittings diagram
    - What is the alloy of steel in the tank? "Steel" is not specific enough.
    (Strictly speaking, we mainly want to know the material of the outlet fitting on the valve.)
    This isn't a huge concern for corrosion, since this will only be installed for days (maybe weeks) at a time.
    - We should probably swap around the "fill hose coupling" and the "tower hose inlet coupling"
    to make the tower hose symmetrical.
    So, there would be no way to put it on backwards.
    This also has the benefit of preventing the fill system from being directly connected
    to the flight system without a hose (which would be dangerou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
2021-08-05 fixed typo
    was: male-male coupling said "female" on the ports
    is: says "male"
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

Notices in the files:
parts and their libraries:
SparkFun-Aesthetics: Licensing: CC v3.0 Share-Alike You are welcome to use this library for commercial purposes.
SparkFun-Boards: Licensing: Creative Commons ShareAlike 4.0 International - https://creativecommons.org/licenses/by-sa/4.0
